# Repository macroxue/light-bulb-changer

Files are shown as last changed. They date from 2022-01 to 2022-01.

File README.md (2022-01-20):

# Light Bulb Changer

https://user-images.githubusercontent.com/1887856/150277999-da080e1b-be22-4c13-8dce-751dee5e4eae.mp4

Check [this Reddit post](https://www.reddit.com/r/functionalprint/comments/s6c34k/changed_light_bulbs_14_feet_above_ground_with_3d/) 
to read what Redditers in [r/functionalprint](https://www.reddit.com/r/functionalprint/) said about this design.

## Parts

* 1/2 in. x 10 ft. PVC schedule 40 pipe. (In retrospect, the pipe is too flexible so 3/4 in. could work better.)
* 6x fingers and 1x wrist, 3D printed
* A piece of electric wire for attaching the fingers to the wrist
* 2x pulleys, 2x tees and 2x stoppers, 3D printed
* A cable to drive the pulleys, e.g. unused phone cable
* M3 bolts
* Rubber bands

## Tools

* 3D printer
* PVC pipe cutter or saw
* Screw driver or Allen wrench

## Build the Hand
changer-hand

3D-print the following pieces. Fast print mode is fine since the pieces don't need to be super precise.
* 6x [finger.stl](https://github.com/macroxue/light-bulb-changer/blob/master/finger.stl)
* 1x [wrist.stl](https://github.com/macroxue/light-bulb-changer/blob/master/wrist.stl)

Put the electric wire through the holes of the wrist and tie its ends. Hook the fingers on to the wire.

Cut about one foot of PVC pipe. Insert the pipe to the socket of the wrist and fasten the assembly with two M3 bolts.

Wrap rubber bands tightly to the tips of the fingers. Put one rubber band through all six holes at the tips and tie its two ends.

## Build the Pulley System
light-bulb-changer

3D-print the following pieces.
* 2x [pulley.stl](https://github.com/macroxue/light-bulb-changer/blob/master/pulley.stl)
* 1x [tee.stl](https://github.com/macroxue/light-bulb-changer/blob/master/tee.stl)
* 1x [tee2.stl](https://github.com/macroxue/light-bulb-changer/blob/master/tee2.stl)
* 2x [stopper.stl](https://github.com/macroxue/light-bulb-changer/blob/master/stopper.stl)

Assemble the pulley system according to the 3D animation above. In my case, the pulleys are about 5 feet apart on a pipe of 7 feet.

Rubber bands can be put in the groove of a pulley to add more grip.

## Adjustment

Since the 1/2 in. PVC pipe was too flexible, it's put inside a stainless steel telescoping pipe savaged from an old clothes rack. In retrospect, the steel pipe alone could be sufficient but I didn't want to redesign the 3D-printed parts.

The hand may be attached to the other end of the pipe so it can change light bulbs in the ceiling or on a celling fan. However, it may not work well for light bulbs with a flat bottom as the fingers can't open eaisly when pushed against the bottom.

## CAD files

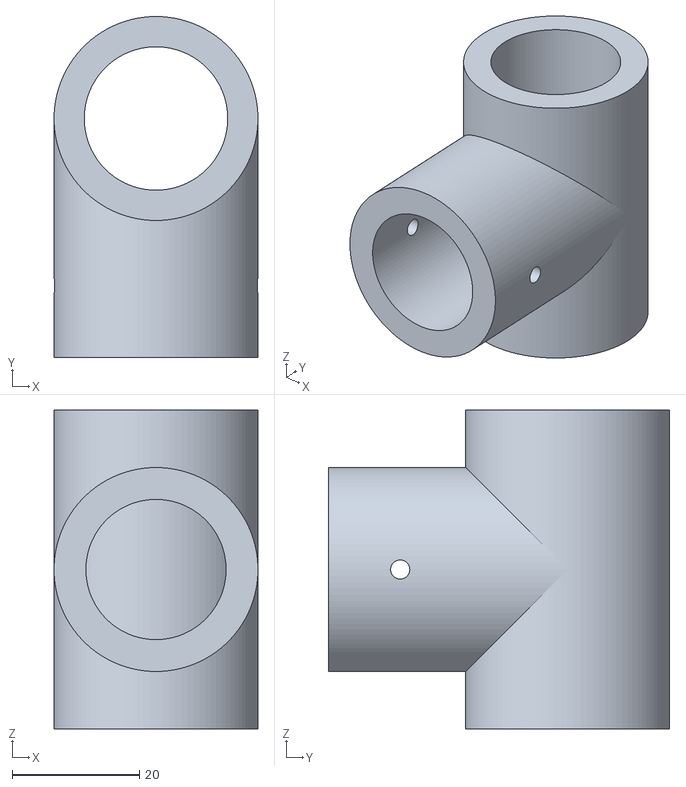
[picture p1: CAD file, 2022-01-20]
tee.stl
32.0 x 53.5 x 50.0

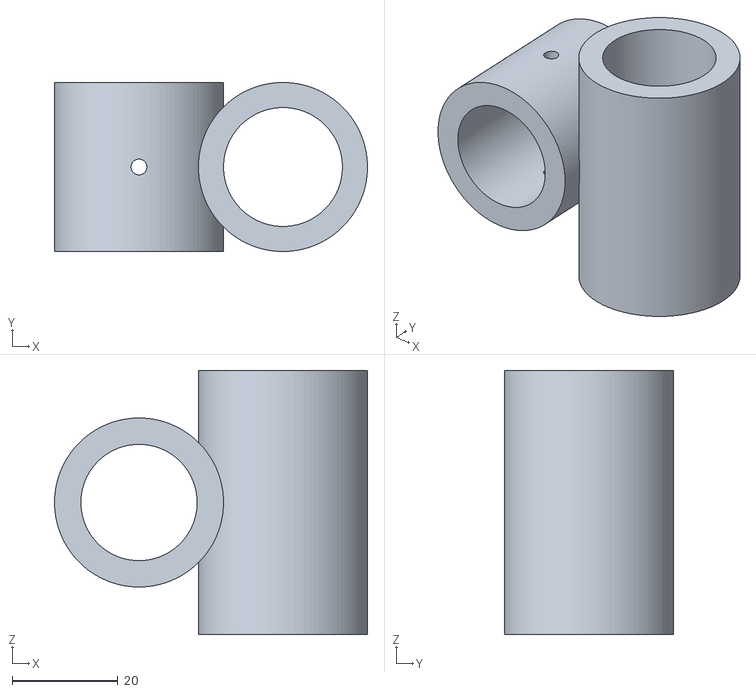
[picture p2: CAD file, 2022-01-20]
tee2.stl
59.2 x 32.0 x 50.0

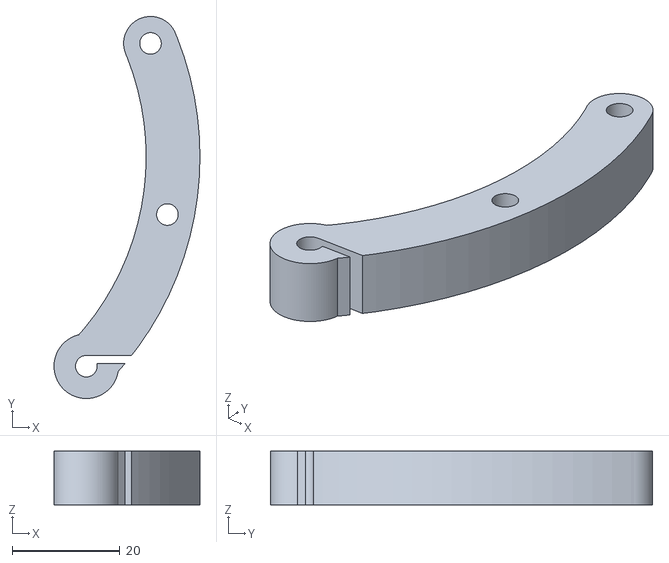
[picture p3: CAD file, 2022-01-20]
finger.stl
27.1 x 70.9 x 10.0

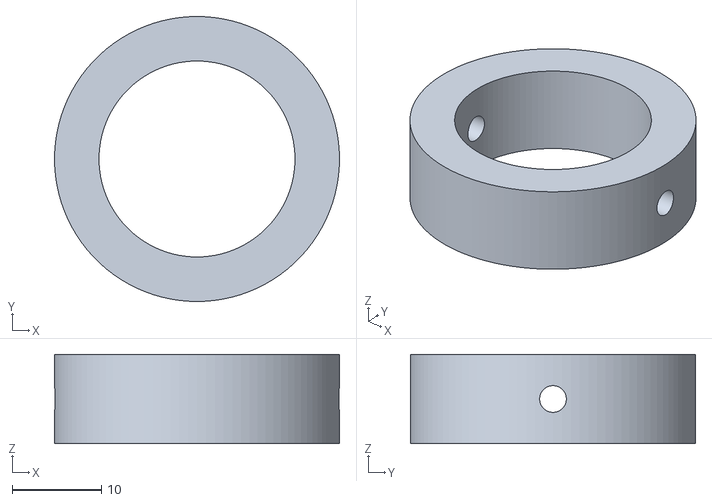
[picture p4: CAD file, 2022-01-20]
stopper.stl
32.0 x 32.0 x 10.0

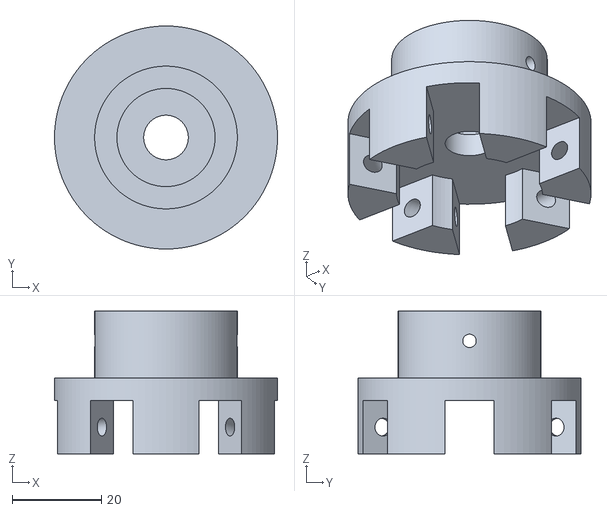
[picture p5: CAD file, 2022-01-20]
wrist.stl
50.0 x 50.0 x 32.0

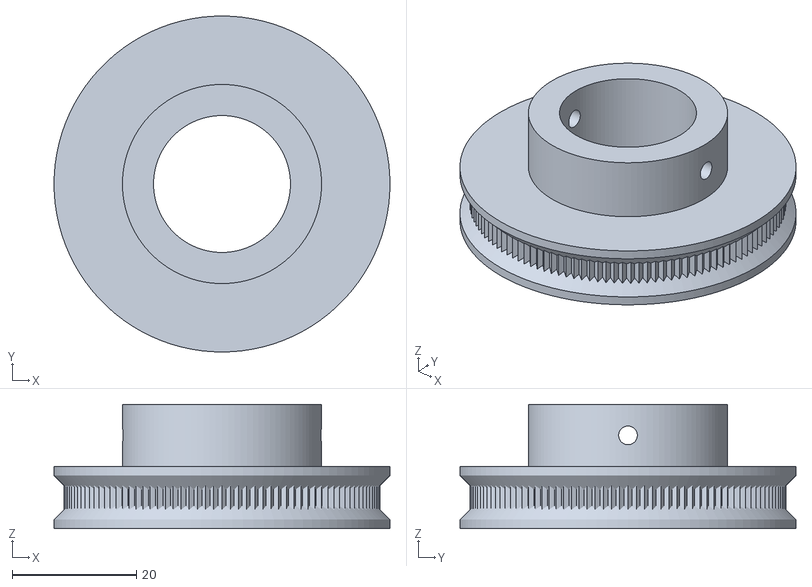
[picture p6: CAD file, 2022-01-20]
pulley.stl
54.0 x 54.0 x 20.0

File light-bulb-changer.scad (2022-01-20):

f = 10;      // finger width
r = 50;      // finger radius
wrist = 20;  // wrist radius
// 3/4 in. x 10 ft. PVC Schedule 40 Plain-End Pipe, $6.46 at Home Depot.
rod = 11;  // rod radius
socket_height = 20;
screw = 3;  // m3
inf = 199;
d = 0.01;
$fn = 100;

module arc(r1, r2, a1, a2) {
  difference() {
    difference() {
      polygon([
        [ 0, 0 ], [ cos(a1) * (r1 + 50), sin(a1) * (r1 + 50) ],
        [ cos(a2) * (r1 + 50), sin(a2) * (r1 + 50) ]
      ]);
      circle(r = r2);
    }
    difference() {
      circle(r = r1 + 100);
      circle(r = r1);
    }
  }
}

module finger_original(end = 22.5) {
  linear_extrude(f) {
    difference() {
      union() {
        translate([ 0, 0, 0 ]) arc(r + f, r, -45, end);
        translate([ (r + f / 2) * cos(-45), (r + f / 2) * sin(-45), 0 ])
            circle(d = f * 1.2);
        translate([ (r + f / 2) * cos(end), (r + f / 2) * sin(end), 0 ])
            circle(d = f * 1);
      }
      mid = (end - 45) / 2;
      translate([ (r + f / 2) * cos(mid), (r + f / 2) * sin(mid), 0 ]) circle(d = 4);
      translate([ (r + f / 2) * cos(-45), (r + f / 2) * sin(-45), 0 ]) circle(d = 4);
      translate([ (r + f / 2) * cos(end), (r + f / 2) * sin(end), 0 ]) circle(d = 4);
    }
  }
}

module finger(end = 22.5) {
  difference() {
    finger_original(end);
    translate([ (r + f / 2) * cos(-45), (r + f / 2) * sin(-45) + 2, -d ])
        rotate([ 0, 0, -90 ]) cube([ 1.5, f, f + d * 2 ]);
  }
}

module wrist() {
  difference() {
    union() {
      difference() {
        cylinder(r = wrist + f / 2, h = f * 1.2);
        for (i = [0:60:360]) {
          rotate([ 0, 0, i ]) translate([ 0, -f / 2 - 0.5, -d ])
              cube([ inf, f + 1, f * 1.2 + d * 2 ]);
        }
        translate([ 0, 0, -d ]) cylinder(r = f * 1.5, h = f * 1.2 + d * 2);
        translate([ 0, 0, f * 1.2 / 2 ]) rotate_extrude() translate([ wrist, 0, 0 ])
            circle(d = 4);
      }
      translate([ 0, 0, -f / 2 ]) cylinder(r = wrist + f / 2, h = f / 2);
      translate([ 0, 0, -socket_height ]) rod_socket();
    }
    cylinder(d = f, h = inf, center = true);
  }
}

module rod_socket() {
  difference() {
    cylinder(r = rod + f / 2, h = socket_height);
    translate([ 0, 0, -f / 2 ]) cylinder(r = rod, h = socket_height);
    translate([ 0, 0, socket_height / 3 ]) rotate([ 0, 90, 0 ])
        cylinder(d = screw, h = inf, center = true);
  }
}

module router_socket(male) {
  difference() {
    union() {
      rotate([ 180, 0, 0 ]) rod_socket();

      // Thread router
      translate([ 0, 0, -4 ]) difference() {
        cylinder(r = rod + f * 1.5, h = 4);
        translate([ 0, 0, -d ]) cylinder(r = rod, h = 4 + d * 2);
        // Thread holes
        for (i = [30:60:360])
          rotate([ 0, 0, i ]) translate([ rod + f, 0, -d ])
              cylinder(d = 4, h = 4 + d * 2);
      }

      // Joint
      translate([ 0, 0, -socket_height - rod - f / 2 ]) difference() {
        union() {
          difference() { sphere(r = rod); }
          cylinder(r = rod, h = rod + f);
        }
        // Screw hole
        translate([ 0, inf / 2, 0 ]) rotate([ 90, 0, 0 ]) cylinder(r = 4, h = inf);
        // Joint
        if (male) {
          translate([ -inf / 2, -(rod / 1.5 + 1) / 2, -inf + rod + f - d ])
              cube([ inf, (rod / 1.5 + 1), inf ]);
        } else {
          translate([ -inf / 2, -rod / 3 - rod / 1.5, -inf + rod + f - d ])
              cube([ inf, rod / 1.5, inf ]);
          translate([ -inf / 2, -rod / 3 + rod / 1.5, -inf + rod + f - d ])
              cube([ inf, rod / 1.5, inf ]);
        }
      }
    }
  }
}

t = 5;
l = 50;

module tee() {
  difference() {
    union() {
      cylinder(r = rod + t, h = l, center = true);
      difference() {
        translate([ 0, -l * 0.375, 0 ]) rotate([ 90, 0, 0 ]) {
          difference() {
            cylinder(r = rod + t, h = l * 0.75, center = true);
            translate([ 0, 0, l * 0.15 ]) rotate([ 0, 90, 0 ])
                cylinder(d = screw, h = inf, center = true);
          }
        }
        translate([ 0, -l / 2, 0 ]) rotate([ 90, 0, 0 ])
            cylinder(r = rod, h = l + d, center = true);
      }
    }
    cylinder(r = rod + 0.25, h = l + d, center = true);
  }
}

module tee2() {
  translate([ rod * 2 + t + 0.25, 0, 0 ]) difference() {
    cylinder(r = rod + t, h = l, center = true);
    cylinder(r = rod + 0.25, h = l + d, center = true);
  }
  rotate([ 90, 0, 0 ]) {
    difference() {
      cylinder(r = rod + t, h = rod * 2 + t * 2, center = true);
      cylinder(r = rod, h = inf, center = true);
      rotate([ 90, 0, 0 ]) cylinder(d = screw, h = inf, center = true);
    }
  }
}

module stopper(height = socket_height / 2) {
  difference() {
    cylinder(r = rod + f / 2, h = height);
    translate([ 0, 0, -d ]) cylinder(r = rod, h = height + d * 2);
    translate([ 0, 0, height * 0.5 ]) rotate([ 0, 90, 0 ])
        cylinder(d = screw, h = inf, center = true);
  }
}

module pulley(radius, height) {
  outer_radius = radius + height * 1.6;
  difference() {
    cylinder(r = outer_radius, h = height, center = true);
    cylinder(r = radius, h = height + d, center = true);
    rotate_extrude() translate([ outer_radius, 0, 0 ]) rotate([ 0, 0, 45 ])
        square(height * .5, center = true);
  }
  for (i = [0:3:360]) {
    rotate([ 0, 0, i ]) translate([ outer_radius - 3, 0, 0 ]) rotate([ 0, 0, 45 ])
        cube([ 2, 2, height ], center = true);
  }
  translate([ 0, 0, height / 2 ]) stopper();
}

module pvc(length) {
  color("#abcdef") difference() {
    cylinder(r = rod, h = length, center = true);
    cylinder(r = rod - 3, h = length + d, center = true);
  }
}

module bulb() {
  color("#fedcba") translate([ 0, 0, 10 ]) {
    sphere(d = 65);
    translate([ 0, 0, 30 ]) rotate([ 0, 180, 0 ])
        linear_extrude(height = 20, scale = 1.5, center = true) {
      circle(r = 15);
    }
  }
}

module candle() {
  color("#fedcba") translate([ 0, 0, 20 ]) cylinder(d = 30, h = 80, center = true);
}

module assembly(degree = 0) {
  // T1
  tee();
  translate([ 0, 0, -f / 2 ]) pvc(l * 2);
  translate([ 0, 0, l * .6 ]) rotate([ 0, 0, degree ]) stopper();

  // T2
  translate([ 0, -l * 4, 0 ]) {
    rotate([ 180, 0, 0 ]) tee2();
    translate([ rod * 2 + t, 0, -f / 2 ]) pvc(l * 2);
    translate([ rod * 2 + t, 0, l * .6 ]) rotate([ 0, 0, degree ]) stopper();
  }

  // Rod connecting T1 and T2
  translate([ 0, -l * 3, 0 ]) rotate([ 90, 0, 0 ]) pvc(l * 5);

  // Pulley1
  pulley_z = -rod - t * 3 - socket_height;
  translate([ 0, 0, pulley_z ]) rotate([ 0, 0, degree ]) pulley(rod, t * 2);

  // Pulley2
  translate([ rod * 2 + t, -l * 4, pulley_z ]) rotate([ 0, 0, degree ])
      pulley(rod, t * 2);

  // Belt
  rotate([ 0, 0, 8 ]) color("#abcdef") {
    translate([ rod + t * 3, 0, pulley_z ]) rotate([ 90, 0, 0 ])
        cylinder(d = t, h = l * 4);
    translate([ -rod - t * 3, 0, pulley_z ]) rotate([ 90, 0, 0 ])
        cylinder(d = t, h = l * 4);
    translate([ 0, 0, pulley_z ]) rotate_extrude(angle = 180)
        translate([ rod + t * 3, 0, 0 ]) circle(d = t);
    translate([ 0, -l * 4, pulley_z ]) rotate([ 180, 0, 0 ]) rotate_extrude(angle = 180)
        translate([ rod + t * 3, 0, 0 ]) circle(d = t);
  }

  // Claw
  translate([ 0, 0, l * 2 + 10 ]) rotate([ 0, 0, degree ]) {
    scale([ 0.8, 0.8, 0.8 ]) bulb();
    for (i = [0:60:360]) rotate([ 0, 0, i ]) {
        translate([ -r * 0.707 + wrist - f / 2, f / 2, 0 ]) rotate([ 90, 0, 0 ]) finger();
      }
    translate([ 0, 0, -r + f / 2 ]) wrist();
  }
}

module pieces() {
  // 6x fingers.
  finger();
  // 1x wrist.
  translate([ t * 3, 0, 0 ]) rotate([ 180, 0, 0 ]) wrist();
  // 2x pulleys.
  translate([ -wrist * 2, 0, 0 ]) pulley(rod, t * 2);
  // 1x tee.
  translate([ t * 2, -wrist * 2 - t, 0 ]) tee();
  // 1x tee2.
  translate([ -wrist * 3, -wrist * 3, 0 ]) tee2();
  // 2x stoppers.
  translate([ wrist * 3 - t, -wrist * 3 - t, 0 ]) stopper(socket_height / 2);
}

module animation() { assembly($t * 360); }

// Uncomment to see the assembly of pieces.
assembly();

// Uncomment to see the rotating plate with OpenScad's "Animate" view.
// animation();

// Uncomment to see pieces to print.
// pieces();
